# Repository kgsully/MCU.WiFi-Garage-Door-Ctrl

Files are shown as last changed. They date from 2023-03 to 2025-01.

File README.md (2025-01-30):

# WiFi Garage Door Controller
ESP32-WROOM Based WiFi enabled garage door controller design.

 Please refer to the README docx or PDF found in the documentation folder for further information.
 
 Schematics and drawings may be found within the documentation folder (dimensions are in mm). 
 
 3D design / printing models are located under the 'Enclosure' folder.

 Design updated for additional endpoint to allow for use with Apple Watch.
 
Imgur

Imgur

Imgur

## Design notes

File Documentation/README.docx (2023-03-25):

WiFi Garage Door Controller

Rev 1.1

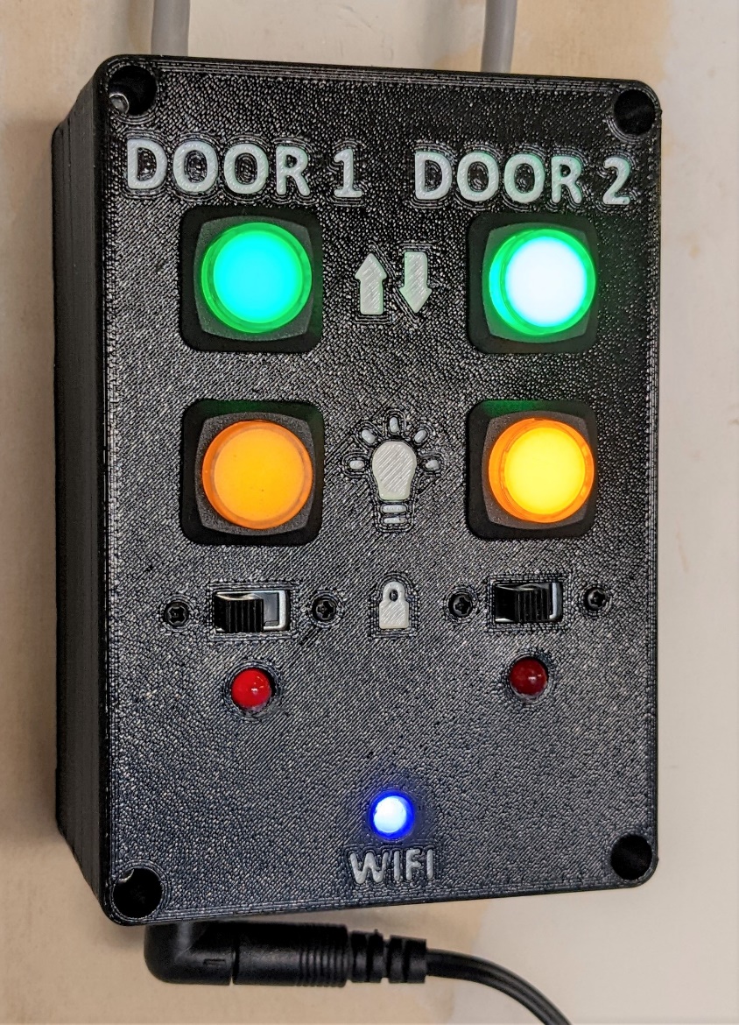
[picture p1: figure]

Ken S. 11/2022

# 1. Description

This is an ESP32-WROOM based design for a WiFi enabled garage door controller capable of operating 2 garage doors. It includes illuminated physical pushbuttons wired in parallel with relays to allow the user to operate the garage doors even if the controller is unpowered or disconnected from WiFi. Included controls mimic those found on the manufacturer provided openers for the units I have – Open/Close, Light On/Off, and Lock. The ESP32 acts as a webserver hosting a website with the applicable controls / status indications for both doors. This project uses the WiFi manager library to aid in WiFi connection and to prevent the need to hard-code the WiFi network credentials into the program. OTA update functionality is also included.

Design files are included for the following:

1. Controller Electrical Schematic (w/ manufacturer and P/N component properties)
2. Controller PCB Layout
3. Interactive PCB Bill of Materials (BOM) – HTML format
4. VS Code / PlatformIO based code
5. 3D Printed Enclosure

# 2. Electrical / PCB

The controller PCB uses 4 reed style relays wired in parallel with physical LED illuminated pushbuttons to control garage door operation. Off board connections use JST-PH style connectors. Please mind polarity (LEDs, etc.) when terminating off-board devices using the male JST-PH connectors.

‘Auto Program’ transistors are included in the design to prevent the need to press the ‘reset’ button after the code is uploaded to the microcontroller. Indication LEDs are generic 5mm THT LEDs.

The manufacturer provided garage door control pad(s) that this design is intended to emulate uses DC voltage only and a voltage divider circuit to determine which button has been pressed / whether the lock switches are set. Please refer to the notes in the addendum or electrical schematic for details. Determination of how your opener works is REQUIRED and resistance values / entire circuit design may need to be changed to accommodate your specific garage door controller!

Note that design accommodation for a UART pin header is included, but not required to be used due to the onboard USB – UART bridge IC.

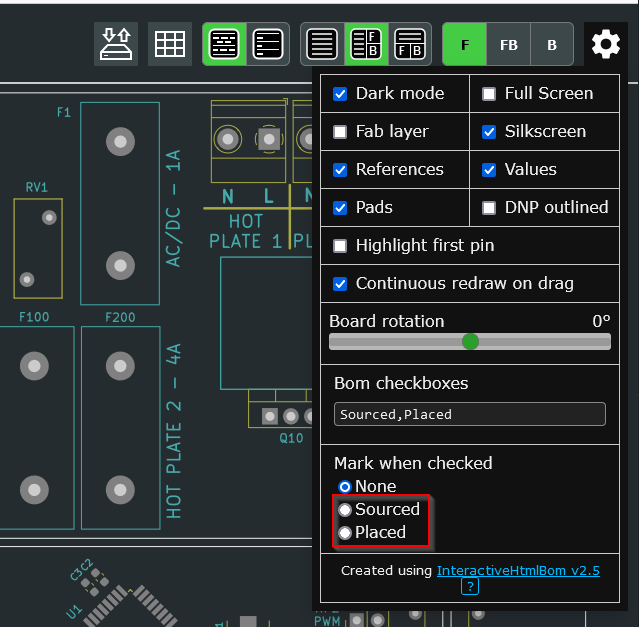
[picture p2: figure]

This design uses a Cypress / Infineon CY7C65213-28PVXI USB – UART bridge IC. The newer CY7C65213A-28PVXI may be used in its place. Please use the configuration utility that can be found at the following URL along with the included configuration file to program the USB – UART bridge:

https://www.infineon.com/cms/en/design-support/tools/configuration/usb-uart-config-utility/

Please refer to the included electrical schematic / PCB design / interactive BOM (html format) for further details. Note that selection of one of the options shown in the screenshot of the interactive BOM may be helpful during PCB assembly –

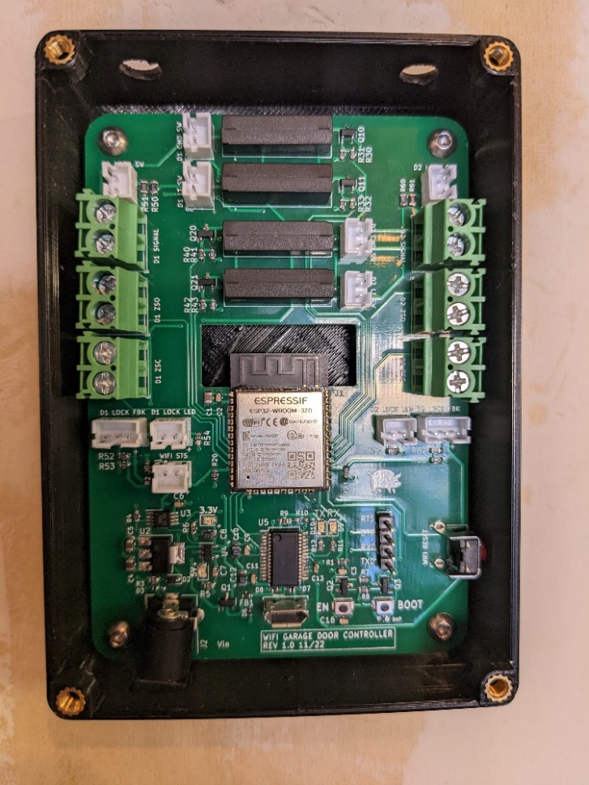
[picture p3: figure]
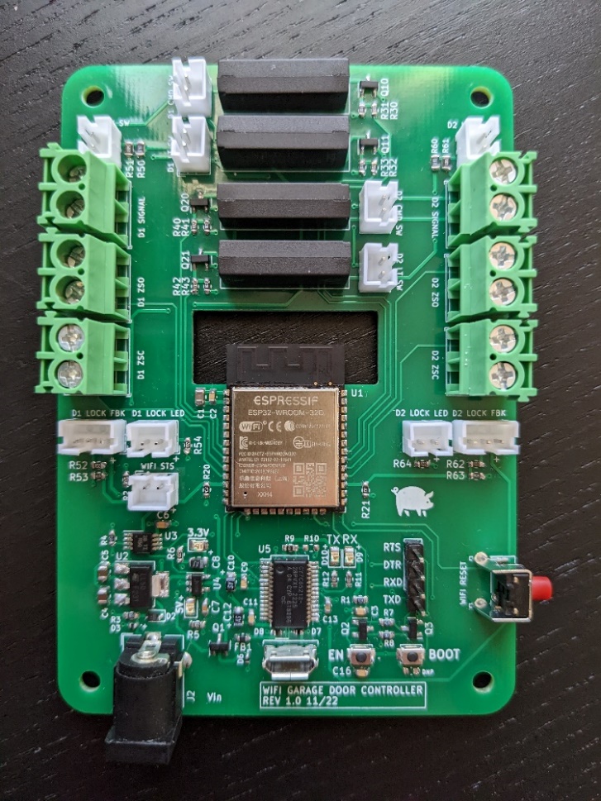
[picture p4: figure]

Completed PCB / Installation Pictures:

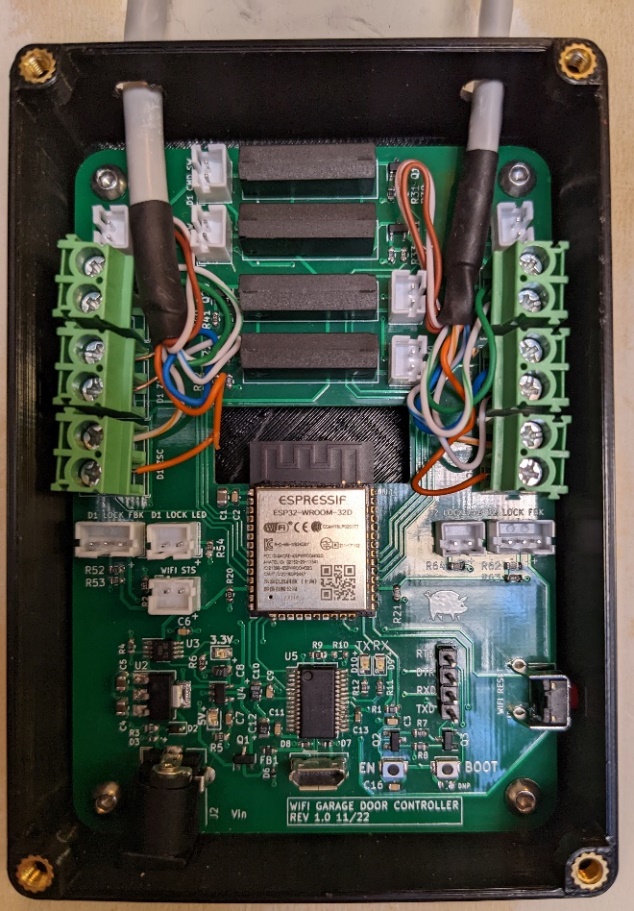
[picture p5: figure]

# 3. Assembly / Construction

Please refer to the included design files for assembly / construction details. Various format 3D models (STEP, F3D, and STL) are included, along with assembly / enclosure component drawings.

Drill holes in top of enclosure bottom of appropriate size for incoming wiring prior to mounting enclosure to the wall. Mount enclosure to the wall prior to mounting PCB in enclosure. CAT5 ethernet cable may be used to provide 8 conductors (2 spare).

NOTE: M3 Threaded heat press inserts are required for PCB mounting holes and enclosure top mounting holes (shown in pictures from previous section). Holes for PCB mounting and enclosure top mounting are sized in the 3D model to accept these inserts – fasteners will not thread into these holes due to their diameters.

# 4. Microcontroller Code

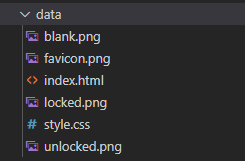
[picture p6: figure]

VS Code / PlatformIO must be used to upload the code to the microcontroller unless the user creates and Arduino IDE version. Note that for upload, there are additional files that must be uploaded to the ESP32 file structure (SPIFFS) – these can be found in the ‘data’ directory in the project. To upload to SPIFFS, select the PlatformIO icon on the left side bar, then select ‘Build’ and then ‘Upload’:

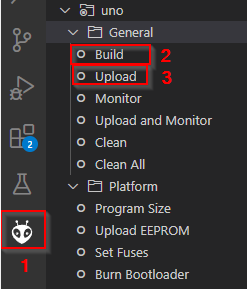
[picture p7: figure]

The code uses the following libraries:

1. Arduino.h
2. WiFi.h
3. ESPAsyncWebServer.h
4. WebSocketsServer.h
5. AsyncElegantOTA.h
6. ArduinoJson.h
7. SPIFFS.h

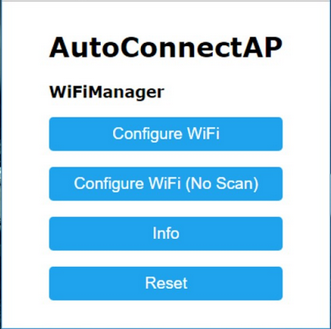
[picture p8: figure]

8. StreamString.h

If a WiFi network has not been configured, upon power up the ESP32 will operate in Access Point (AP) mode and hosts a website that scans for available WiFi networks and allows the user to select and provide credentials to connect. Once saved, this information is retained by the ESP32, even after a power cycle. It is suggested to set a static IP address for the ESP32 in your router configuration to ensure the IP address always remains the same.
The WiFi manager portal is configured to use the default http port of 80 for ease of use and connection.

There is a ‘WiFi’ reset button included in the design on the right side of the PCB that when pressed, will reset the WiFi connection configuration and re-enable WiFi manager.

Once connected to a WiFi network, WiFi manager will be disabled and the ESP32 will operate in station mode and automatically connect to the configured WiFi network upon power up.

The web page used for control and monitoring uses port 8080. This site is hosted by the ESP32 and can be modified by updating the index.html and style.css files contained in the project. It uses web sockets to pass JSON messages between the web page and the control code running in the ESP32. The web sockets server is set to use port 8081.

# 5. Operation / Usage

The controller can be powered via the 2.1mm barrel jack connector with a readily available 9VDC or 12VDC AC to DC converter - Ensure correct polarity of jack connection before purchase (positive on the inside).

The physical pushbuttons may be used in parallel with the web page to control garage door functions. Note that the lock functionality can only be toggled with the physical switch.

Control Over WiFi -

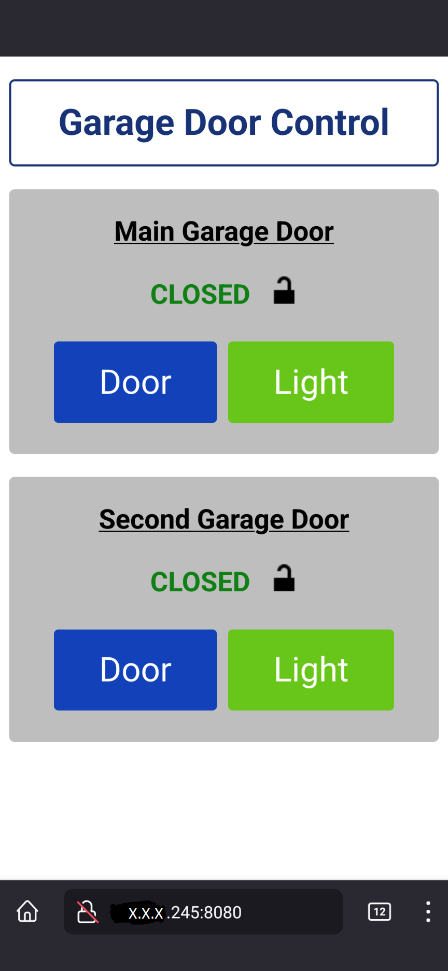
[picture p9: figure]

To connect to the control web page, navigate in a browser (computer or mobile device) to the IP address of the controller with the port suffix ‘:8080’ (e.g. 192.168.1.245:8080 - see screenshot).

Indicators / controls on the web page allow the user to monitor the current open or closed state of the garage door, whether the lock switch is set, and buttons are provided to issue an open / close command (‘Door’ button) or turn the light on or off (‘Light’ button). If the limit switches are in a state where neither is made, the indicator will display ‘Transition’, if both switches are made simultaneously, it will display ‘FAULT’.

If your device has been disconnected from the WiFi network the garage door controller is connected to, a page refresh may be required for status to update / commands to issue to the controller.

OTA Updates –

Program code as well as SPIFFS file system files can be updated ‘Over the Air’ (OTA) without the requirement to connect via USB. The file format required for OTA updates (both program and SPIFFS files) is .bin and must be created from the IDE before upload.

To use the OTA Update function, navigate to the IP_Address:Port (8080)/update (e.g. 192.168.1.245:8080/update - see screenshot).

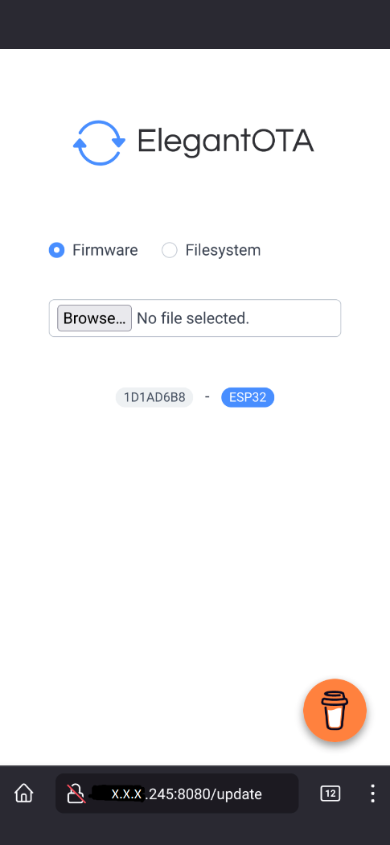
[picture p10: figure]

# 6. Addendum

Door Interface Notes:

Measured Voltages:
Door 1: ~ 5 VDC (No AC)
Door 2: ~ 18 VDC (No AC)

Measured Resistances (same for both doors):
Unlocked:
No Buttons Open Line
Command Button < 1 ohm (short)
Light Button ~ 204 ohms

Locked:
No Buttons ~83 ohms
Command Button < 1 ohm (short)
Light Button ~ 83 ohms

Links / Part Numbers for various off-board / supporting parts:

DC Barrel Jack Connector – 2.1mm:
Adafruit PID 373
https://www.adafruit.com/product/373

Door Switches (Green):
Adafruit PID 1440
https://www.adafruit.com/product/1440

Door Switches (Yellow / Amber):
Adafruit PID 1441
https://www.adafruit.com/product/1441

Lock Slide Switches:
Nidec Copal - MFS201N-Z
https://www.digikey.com/en/products/detail/nidec-copal-electronics/MFS201N-Z/5086556

Door Limit Switches (Generic):
https://a.co/d/92kAZzZ

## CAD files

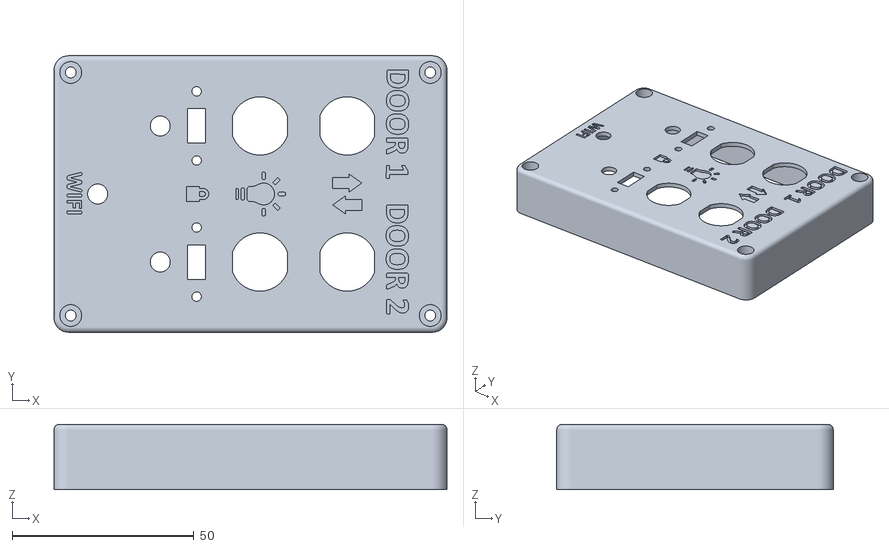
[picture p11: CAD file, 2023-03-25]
Enclosure/3D Printing/Model/Enclosure_Top.stl
108.0 x 76.0 x 18.0

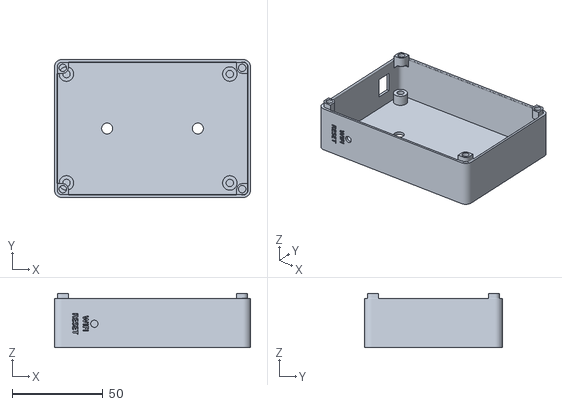
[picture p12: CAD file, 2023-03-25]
Enclosure/3D Printing/Model/Enclosure_Bottom.stl
108.0 x 76.0 x 30.0

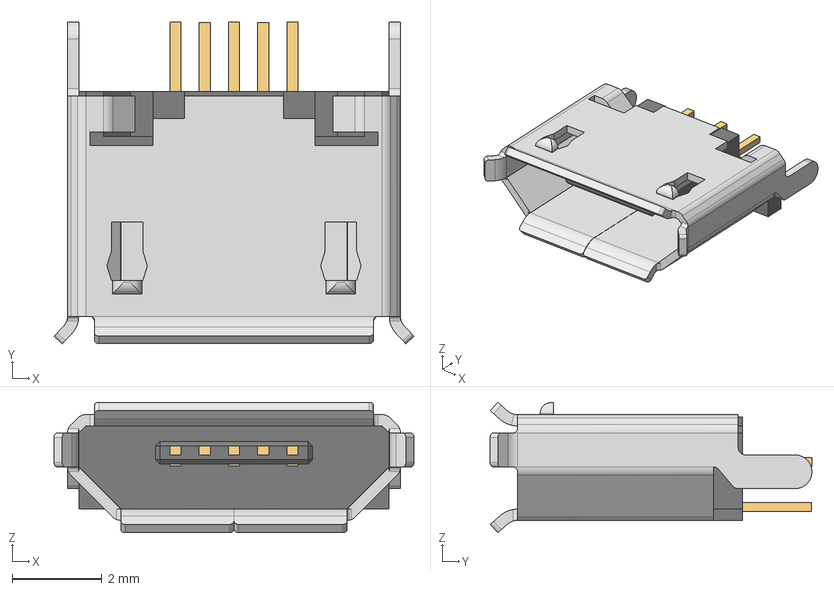
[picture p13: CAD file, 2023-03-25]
Electrical & PCB/Models/614105150721 (rev1).stp
8.00 x 7.15 x 2.90 mm
614105150721_Housing
614105150721_Pin1 x 3
614105150721_Pin2 x 2
614105150721_Shielding

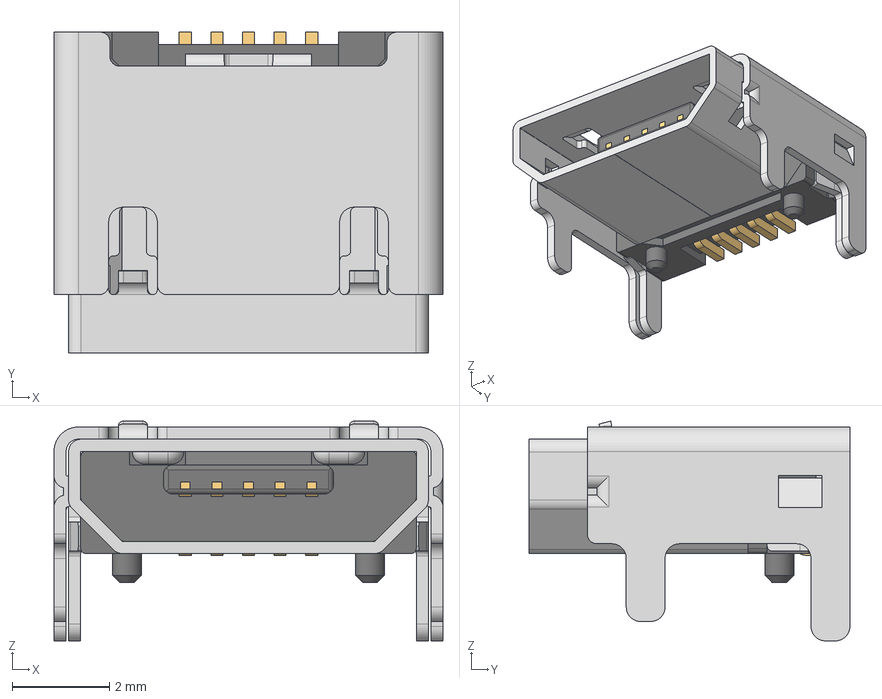
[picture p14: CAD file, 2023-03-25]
Electrical & PCB/Models/629105150521 (rev1).stp
8.00 x 6.60 x 4.52 mm
629105150521_Housing
629105150521_Pin1 x 4
629105150521_Pin2
629105150521_Shielding2
629105150521_Shielding

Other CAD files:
Enclosure/Model/Garage Door Controller Enclosure.f3d

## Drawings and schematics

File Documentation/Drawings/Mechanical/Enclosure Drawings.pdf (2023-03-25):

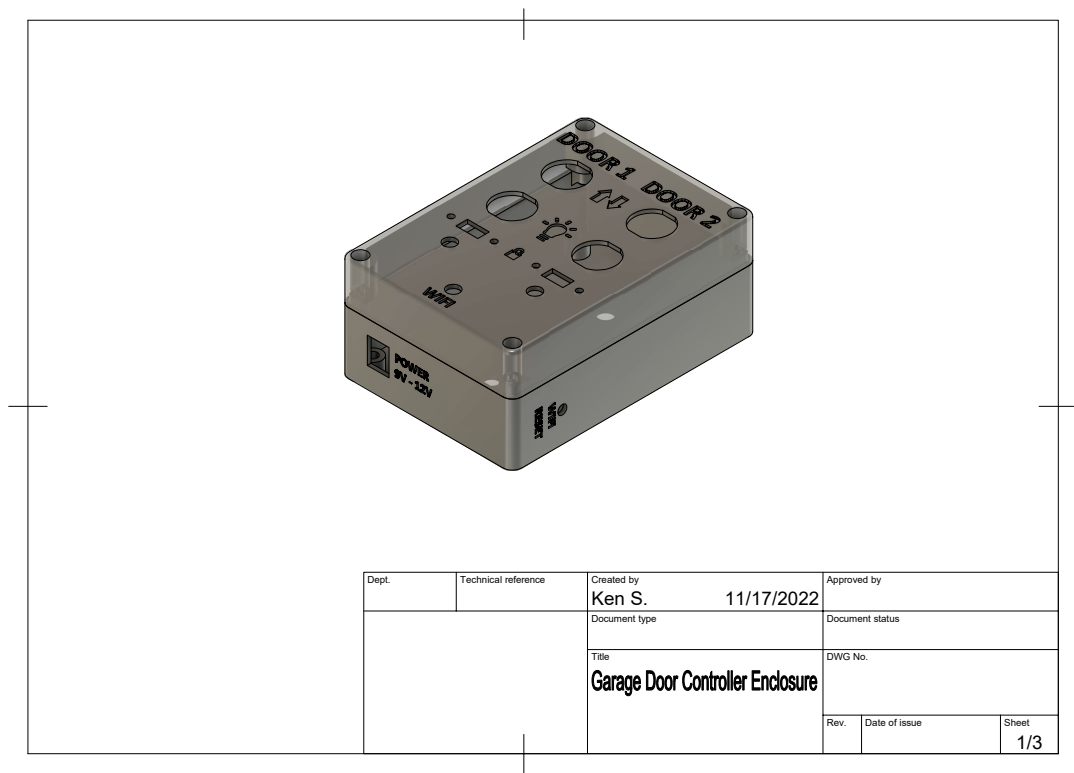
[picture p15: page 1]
Dept.; Technical reference; Created by; Approved by Document type; Document status Title; DWG No. Rev.; Date of issue; Sheet 11/17/2022; 1/3 Ken S.

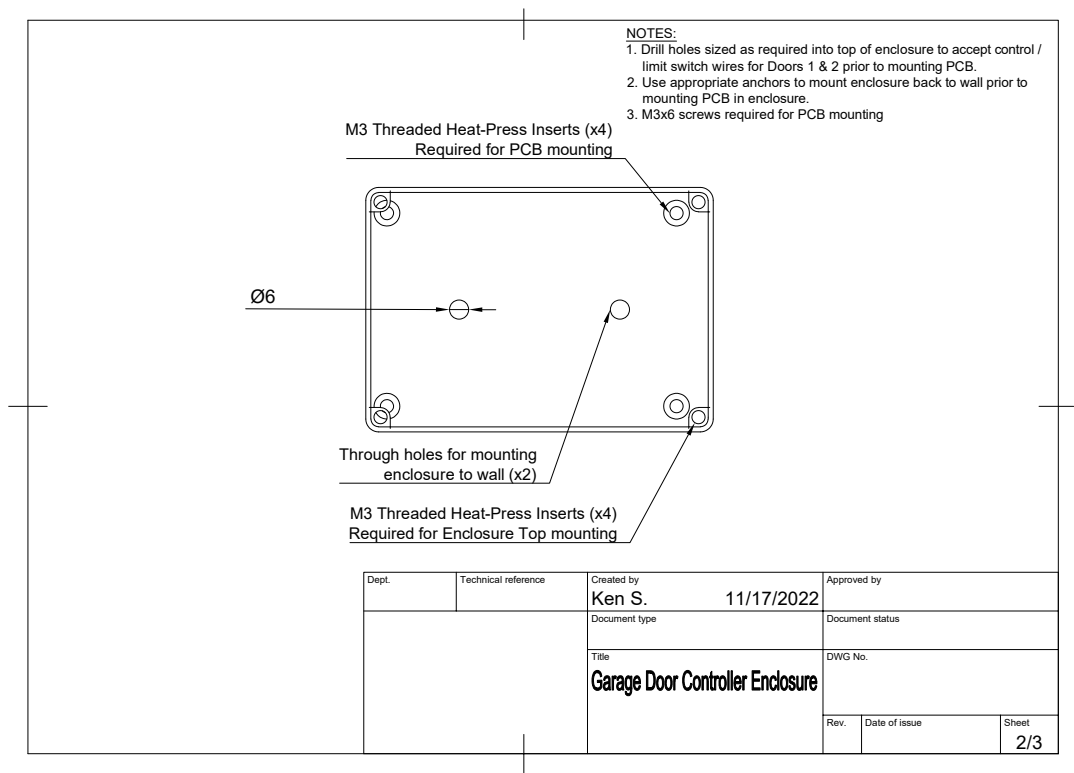
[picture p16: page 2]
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

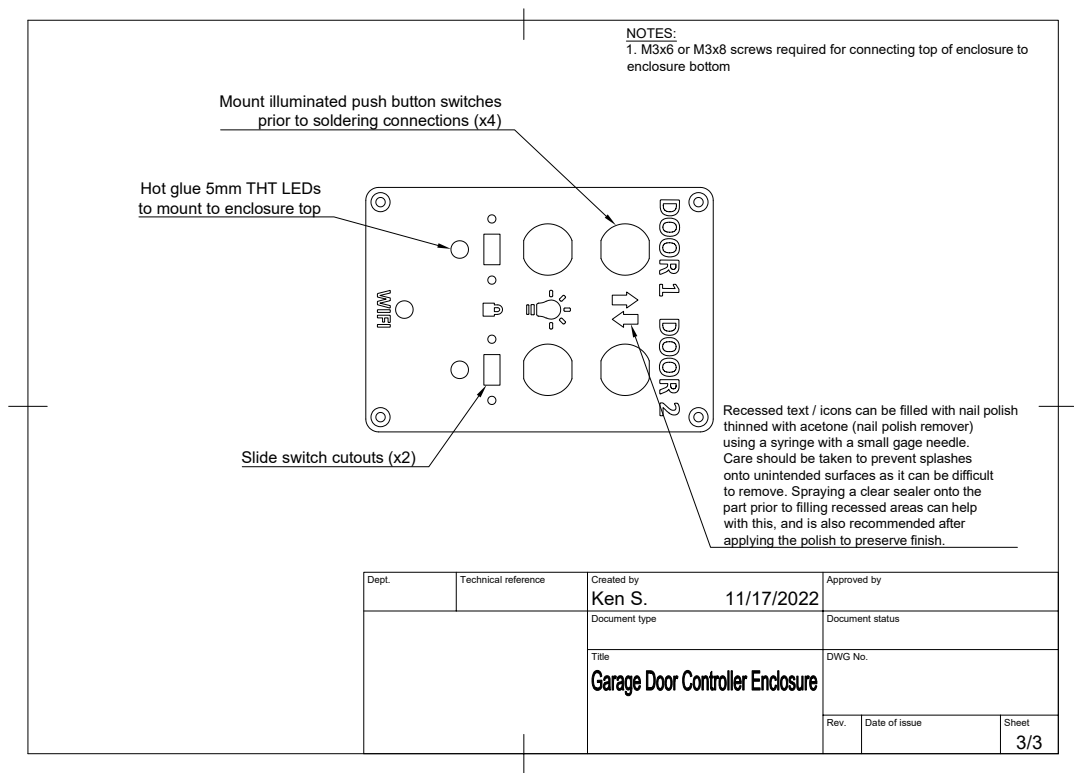
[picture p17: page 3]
Dept.; Technical reference; Created by; Approved by Document type; Document status Title; DWG No. Rev.; Date of issue; Sheet 11/17/2022; 3/3 Ken S. Mount illuminated push button switches prior to soldering connections (x4) Slide switch cutouts (x2) Hot glue 5mm THT LEDs to mount to enclosure top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

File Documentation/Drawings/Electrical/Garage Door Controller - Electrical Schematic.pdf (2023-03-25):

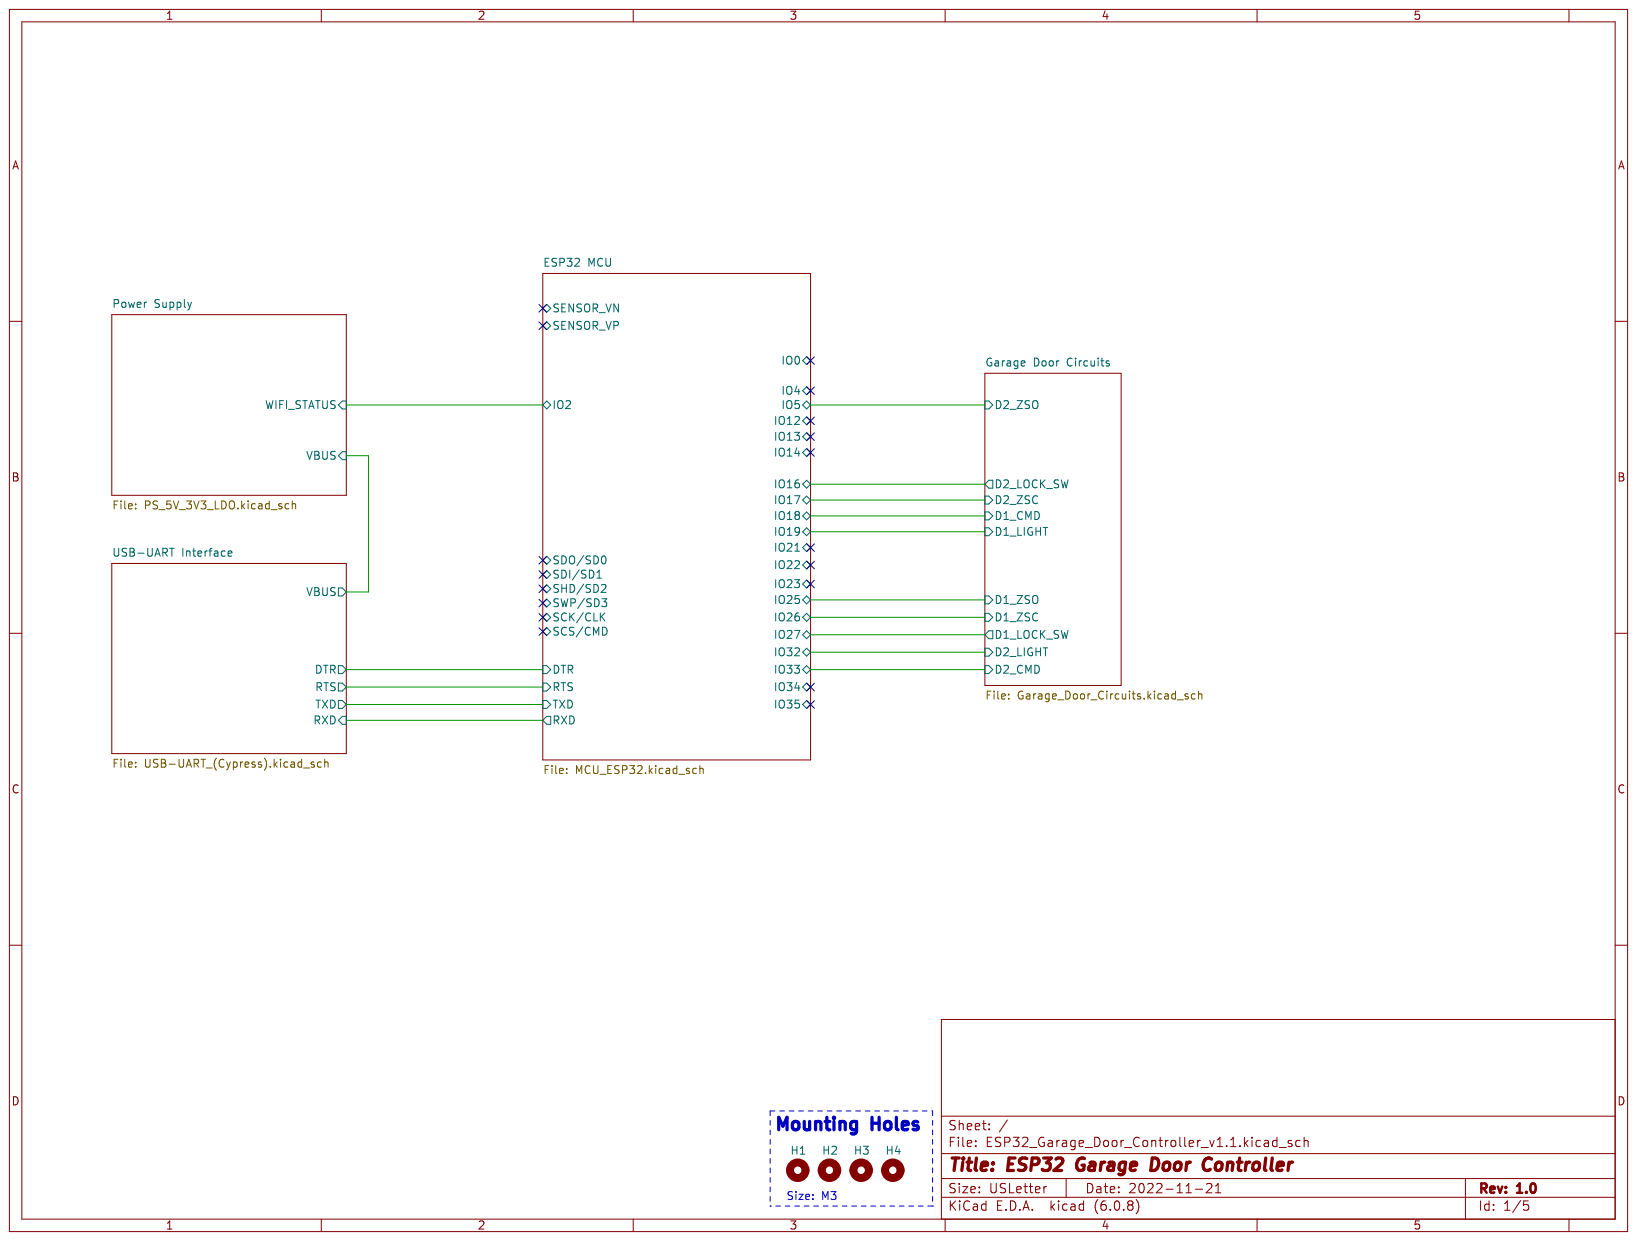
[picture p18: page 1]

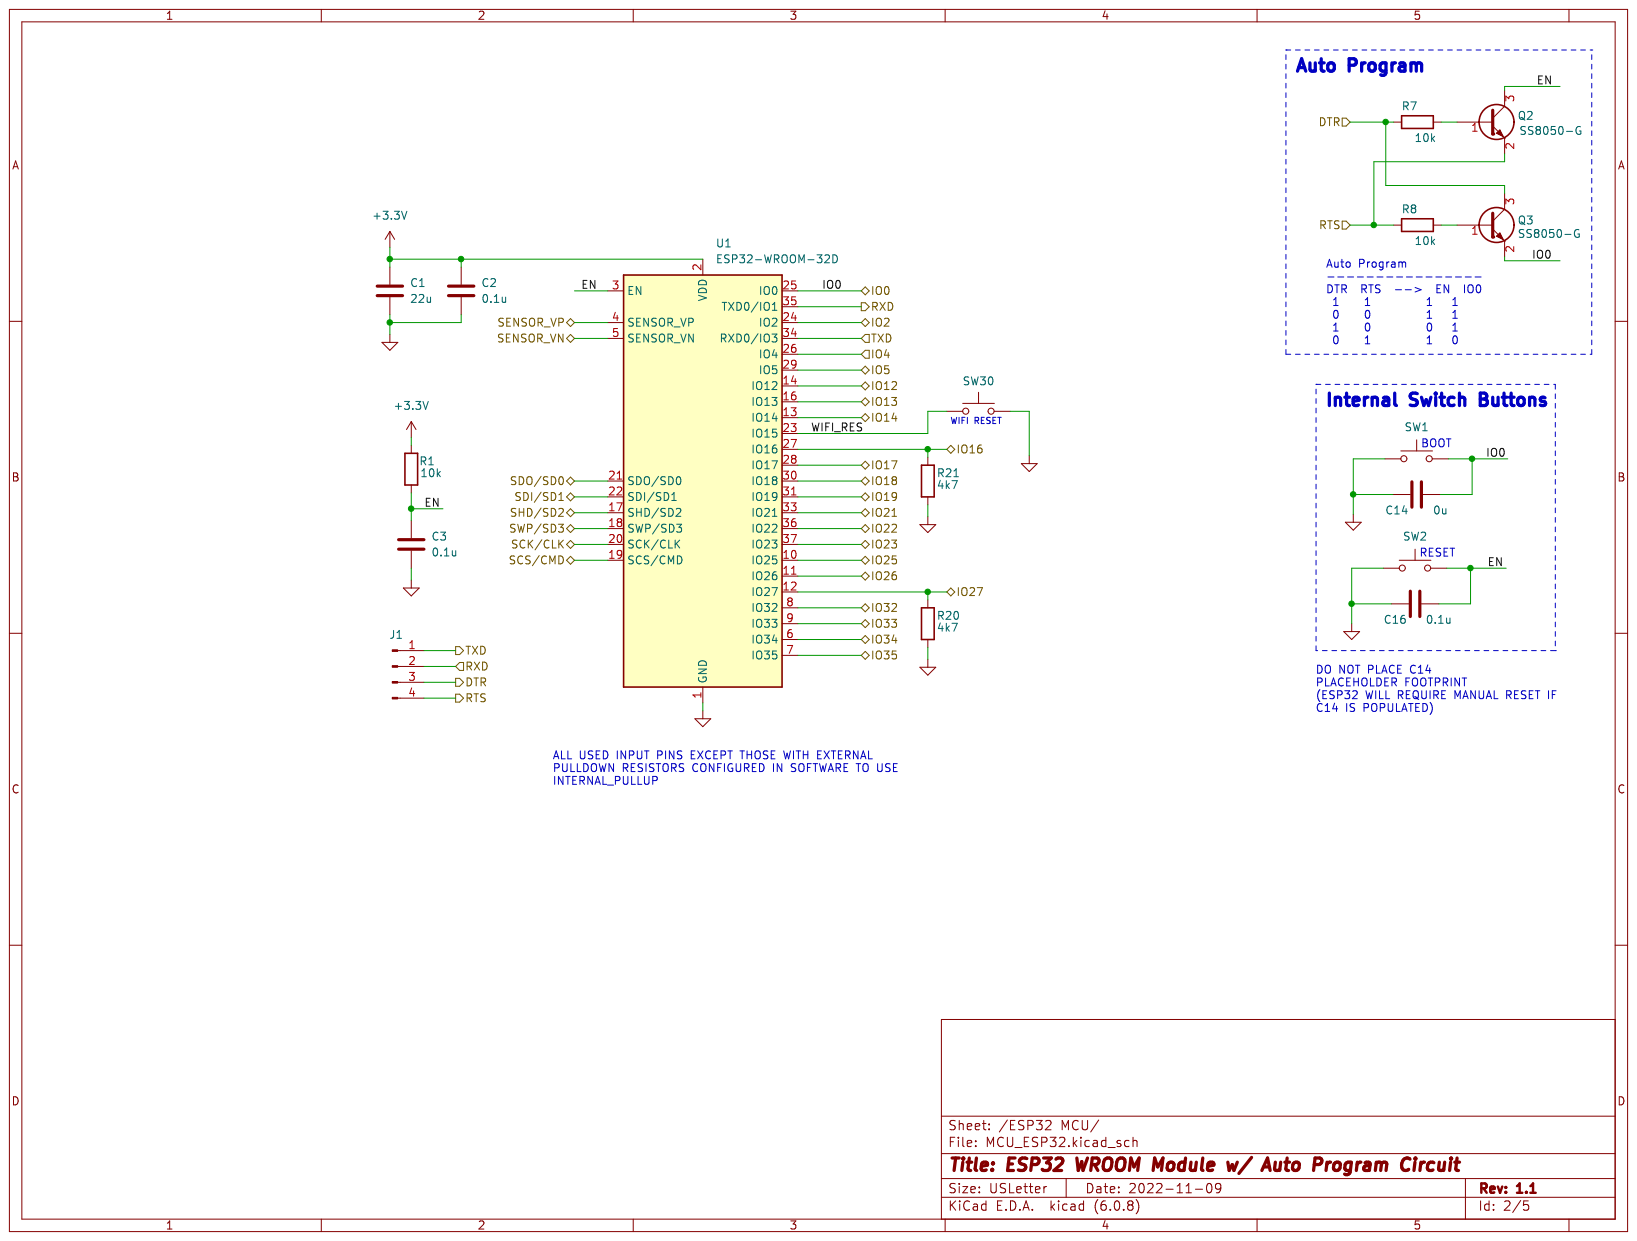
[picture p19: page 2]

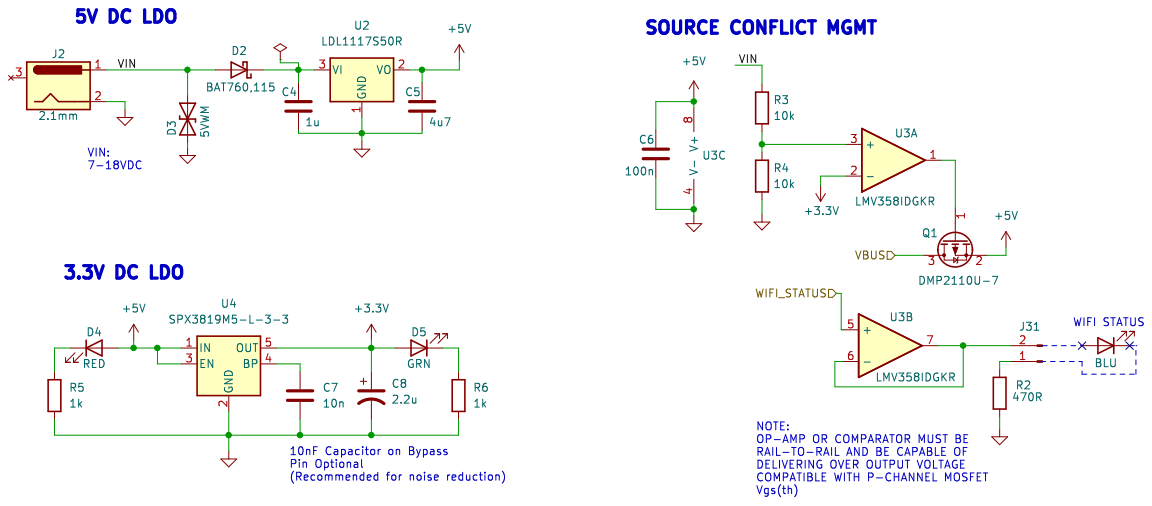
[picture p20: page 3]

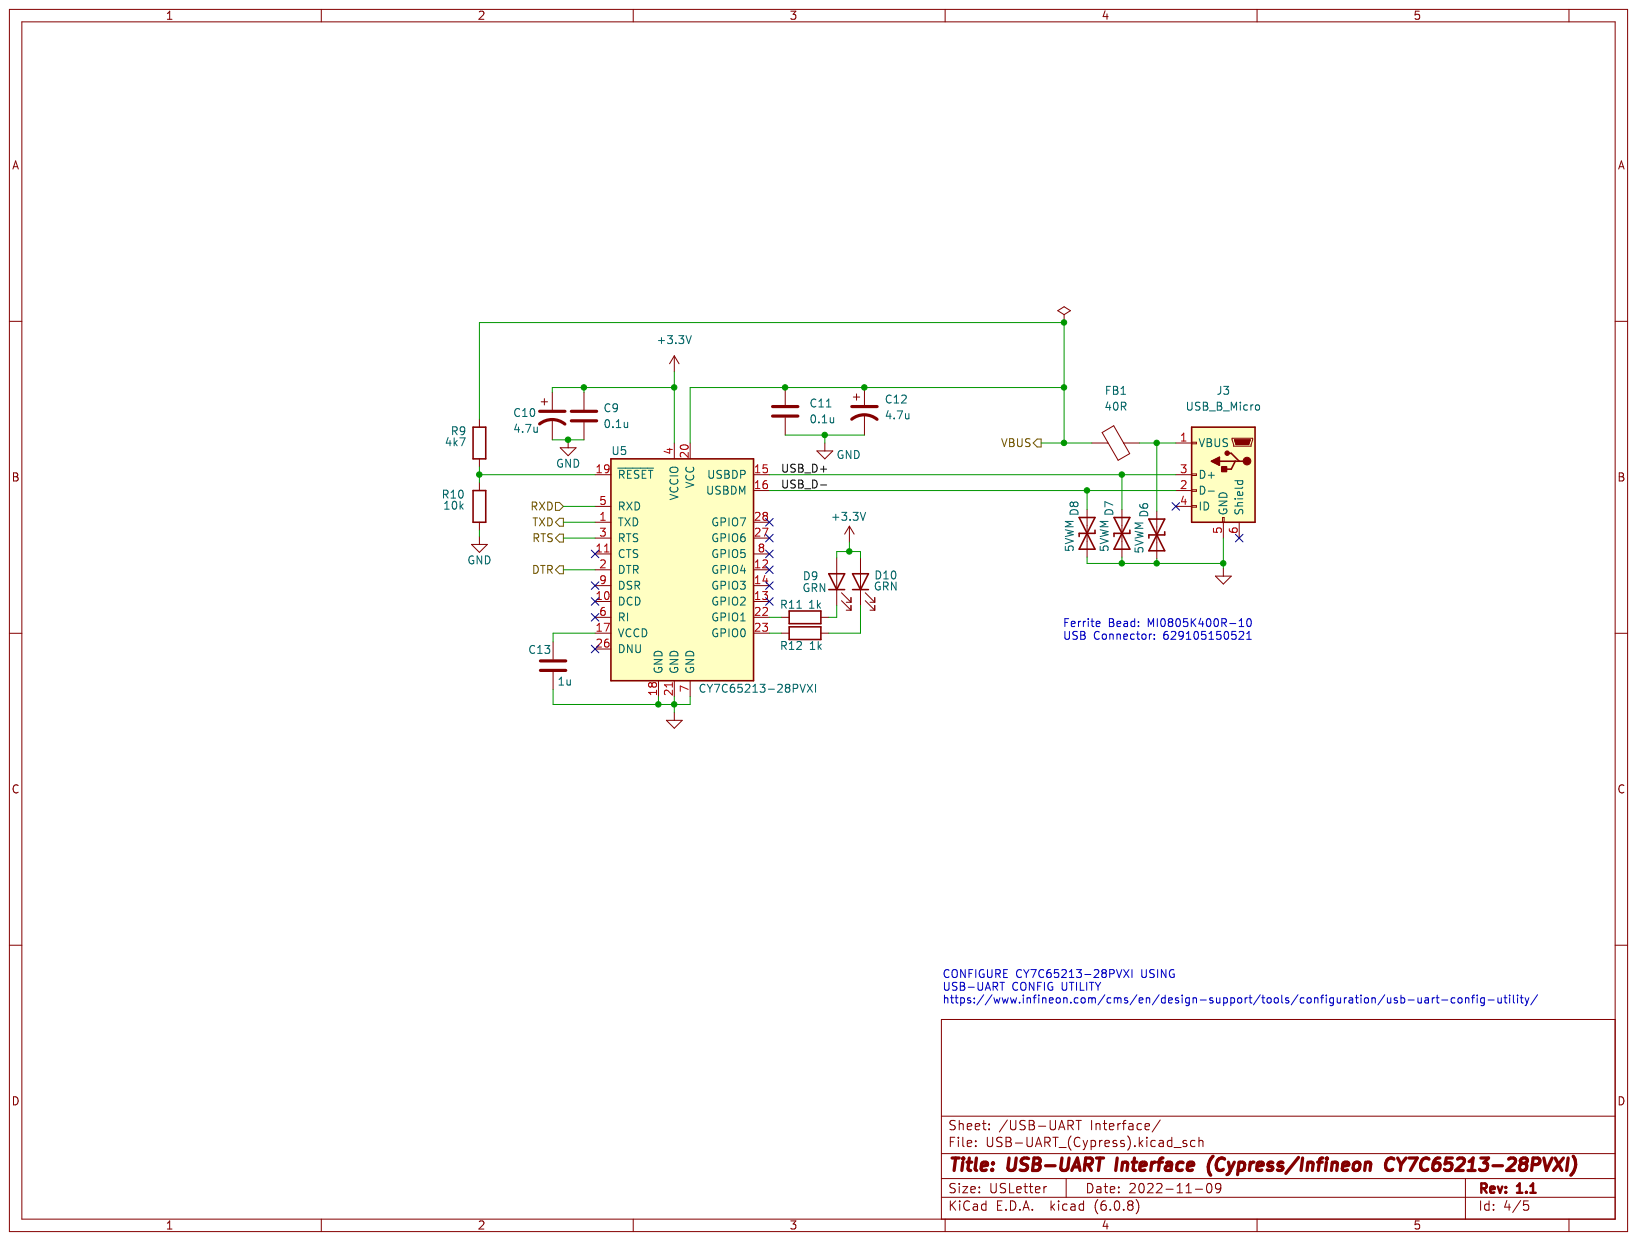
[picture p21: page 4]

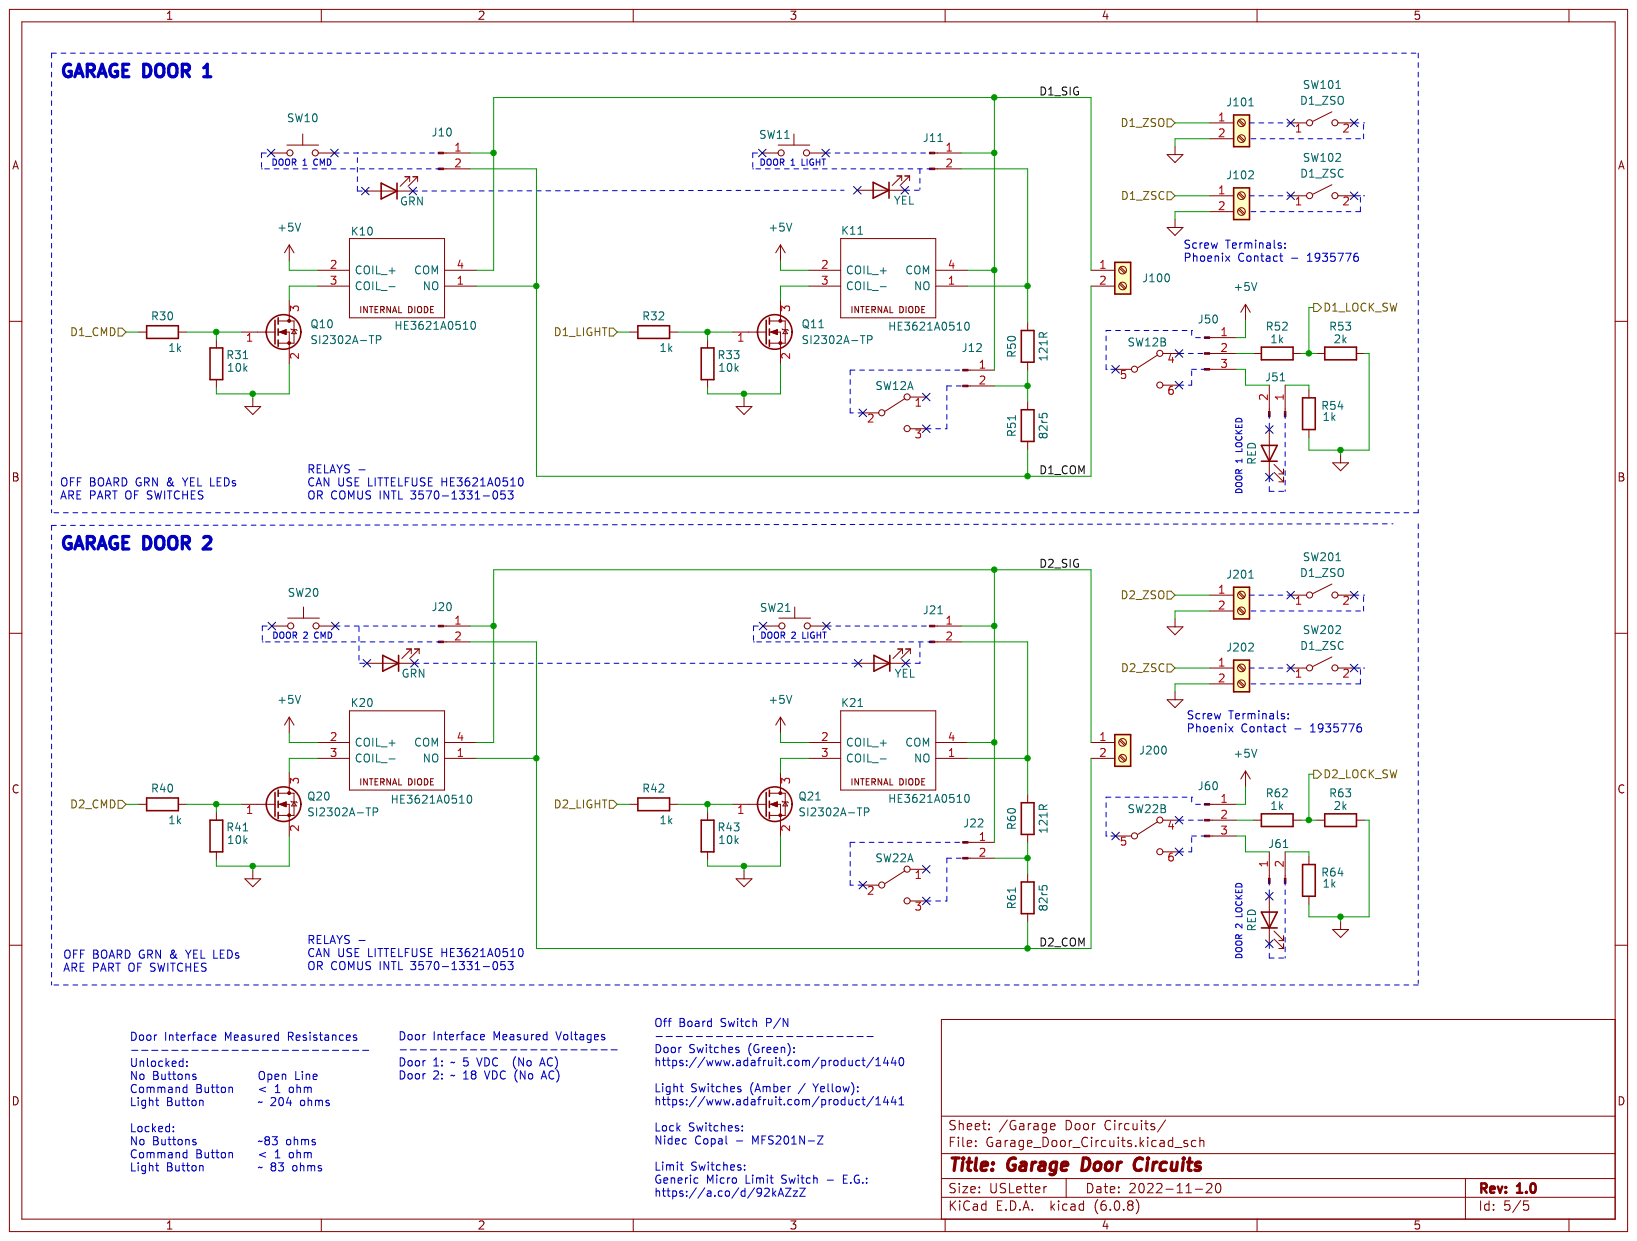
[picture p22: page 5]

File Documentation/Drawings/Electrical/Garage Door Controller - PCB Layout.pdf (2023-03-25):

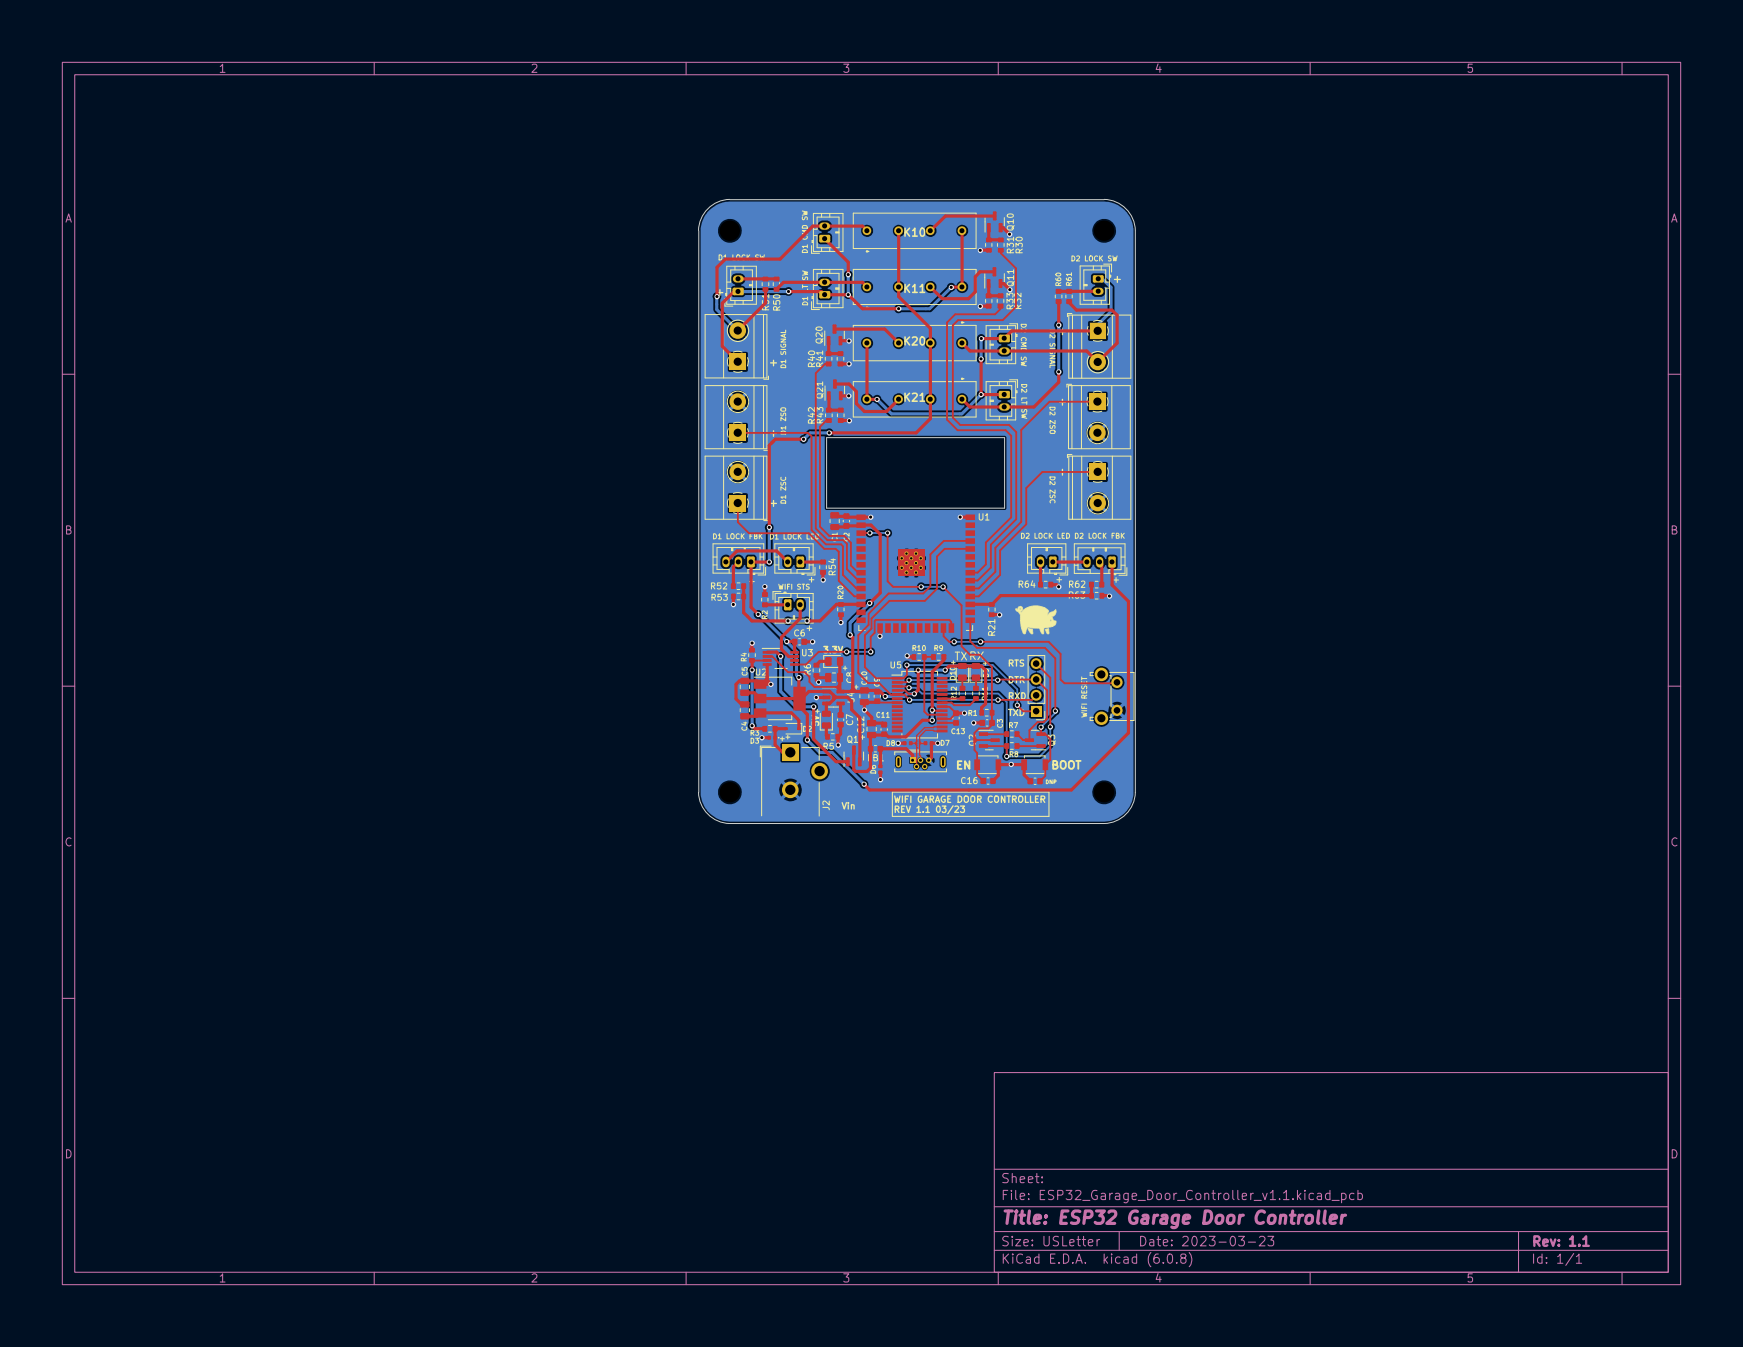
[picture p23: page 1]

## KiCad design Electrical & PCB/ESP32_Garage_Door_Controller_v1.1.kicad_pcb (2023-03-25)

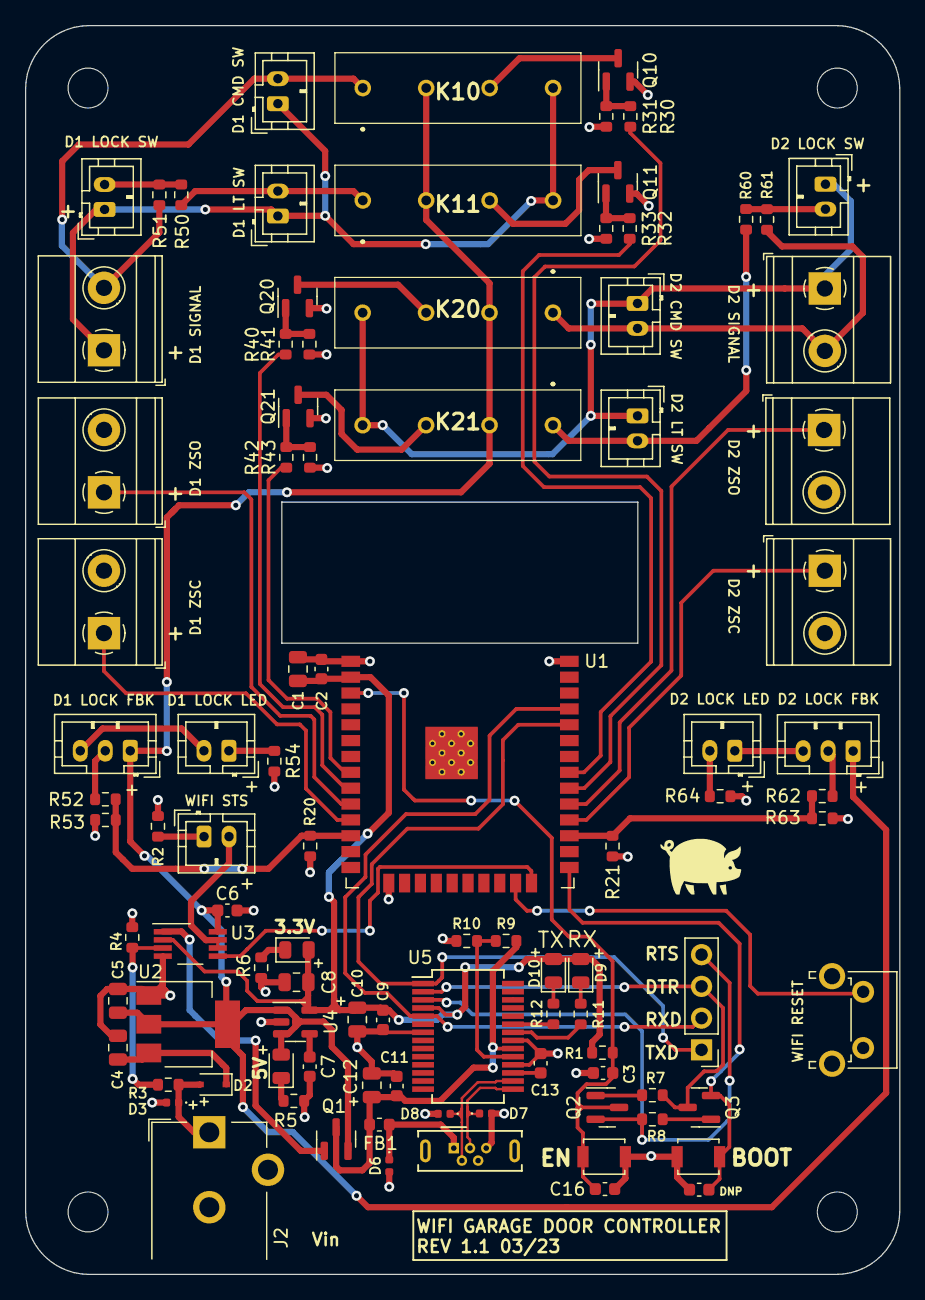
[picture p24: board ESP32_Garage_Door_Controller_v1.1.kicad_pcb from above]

Board: 2 copper layers, 70.0 x 100.0 mm, 100 parts (0 on the bottom side), 64 nets.

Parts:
C1: 22u; C_0805_2012Metric
C2, C3, C9, C11, C16: 0.1u; C_0603_1608Metric
C4: 1u; C_0805_2012Metric
C5: 4u7; C_0805_2012Metric
C6: 100n; C_0603_1608Metric
C7: 10n; C_0603_1608Metric
C8: 2.2u; C_0805_2012Metric
C10, C12: 4.7u; C_0805_2012Metric
C13: 1u; C_0603_1608Metric
C14: 0u; C_0603_1608Metric
D2: BAT760,115; D_SOD-323
D3, D6, D7, D8: 5VWM; D_0402_1005Metric
D4: RED; LED_0805_2012Metric
D5, D9, D10: GRN; LED_0805_2012Metric
FB1: 40R; L_0603_1608Metric
H1, H2, H3, H4: MountingHole; MountingHole_3.2mm_M3
J1: Conn_01x04_Male; PinHeader_1x04_P2.54mm_Vertical
J2: 2.1mm; BarrelJack_CUI_PJ-102AH_Horizontal
J3: USB_B_Micro; USB_Micro-B_Wuerth_614105150721_Vertical
J10, J11, J12, J20, J21, J22, J31, J51, J61: Conn_01x02_Male; JST_PH_B2B-PH-K_1x02_P2.00mm_Vertical
J50, J60: Conn_01x03_Male; JST_PH_B3B-PH-K_1x03_P2.00mm_Vertical
J100, J101, J102, J200, J201, J202: 1935776; TerminalBlock_Phoenix_MKDS-1,5-2_1x02_P5.00mm_Horizontal
K10, K11, K20, K21: HE3621A0510
Q1: DMP2110U-7; SOT-23
Q2, Q3: SS8050-G; SOT-23
Q10, Q11, Q20, Q21: SI2302A-TP; SOT-23
R1, R3, R4, R7, R8, R10, R31, R33, R41, R43: 10k; R_0603_1608Metric
R2: 470R; R_0603_1608Metric
R5, R6, R11, R12, R30, R32, R40, R42, R52, R54, R62, R64: 1k; R_0603_1608Metric
R9, R20, R21: 4k7; R_0603_1608Metric
R50, R60: 121R; R_0603_1608Metric
R51, R61: 82r5; R_0603_1608Metric
R53, R63: 2k; R_0603_1608Metric
SW1, SW2: SW_Push; SW_SPST_B3U-1000P
SW30: SW_Push; SW_Tactile_SPST_Angled_PTS645Vx58-2LFS
U1: ESP32-WROOM-32D; ESP32-WROOM-32
U2: LDL1117S50R; SOT-223-3_TabPin2
U3: LMV358IDGKR; VSSOP-8_3.0x3.0mm_P0.65mm
U4: SPX3819M5-L-3-3; SOT-23-5
U5: CY7C65213-28PVXI; SSOP-28_5.3x10.2mm_P0.65mm

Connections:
+3.3V: C1.1, C2.1, C8.1, C9.2, C10.1, D5.2 (A), D9.2 (A), D10.2 (A), R1.1, U1.2 (VDD), U3.2 (-), U4.5 (OUT), U5.4 (VCCIO)
+5V: C5.1, C6.1, D4.2 (A), J50.1, J60.1, K10.2 (COIL_+), K11.2 (COIL_+), K20.2 (COIL_+), K21.2 (COIL_+), Q1.2 (S), U2.2 (VO), U3.8 (V+), U4.1 (IN), U4.3 (EN)
/ESP32 MCU/DTR: J1.3, Q3.3 (C), R7.1, U5.2 (DTR)
/ESP32 MCU/EN: C3.1, C16.2, Q2.3 (C), R1.2, SW2.2, U1.3 (EN)
/ESP32 MCU/IO0: C14.2, Q3.2 (E), SW1.2, U1.25 (IO0)
/ESP32 MCU/IO2: U1.24 (IO2), U3.5 (+)
/ESP32 MCU/IO5: J201.1, U1.29 (IO5)
/ESP32 MCU/IO16: R21.1, R62.1, R63.2, U1.27 (IO16)
/ESP32 MCU/IO17: J202.1, U1.28 (IO17)
/ESP32 MCU/IO18: R30.1, U1.30 (IO18)
/ESP32 MCU/IO19: R32.1, U1.31 (IO19)
/ESP32 MCU/IO25: J101.1, U1.10 (IO25)
/ESP32 MCU/IO26: J102.1, U1.11 (IO26)
/ESP32 MCU/IO27: R20.1, R52.1, R53.2, U1.12 (IO27)
/ESP32 MCU/IO32: R42.1, U1.8 (IO32)
/ESP32 MCU/IO33: R40.1, U1.9 (IO33)
/ESP32 MCU/RTS: J1.4, Q2.2 (E), R8.2, U5.3 (RTS)
/ESP32 MCU/RXD: J1.2, U1.35 (TXD0/IO1), U5.5 (RXD)
/ESP32 MCU/TXD: J1.1, U1.34 (RXD0/IO3), U5.1 (TXD)
/ESP32 MCU/WIFI_RES: SW30.1, U1.23 (IO15)
/Garage Door Circuits/D1_COM: J10.2, J100.2, K10.1 (NO), R51.1
/Garage Door Circuits/D1_SIG: J10.1, J11.1, J12.1, J100.1, K10.4 (COM), K11.4 (COM)
/Garage Door Circuits/D2_COM: J20.2, J200.2, K20.1 (NO), R61.1
/Garage Door Circuits/D2_SIG: J20.1, J21.1, J22.1, J200.1, K20.4 (COM), K21.4 (COM)
/Power Supply/VBUS: C11.2, C12.1, FB1.2, Q1.3 (D), R9.2, U5.20 (VCC)
/Power Supply/VIN: D2.2 (A), D3.1 (A1), J2.1, R3.1
/USB-UART Interface/USB_D+: D7.1 (A1), J3.3 (D+), U5.15 (USBDP)
/USB-UART Interface/USB_D-: D8.1 (A1), J3.2 (D-), U5.16 (USBDM)
GND: C1.2, C2.2, C3.2, C4.2, C5.2, C6.2, C7.2, C8.2, C9.1, C10.2, C11.1, C12.2, C13.2, C14.1, C16.1, D3.2 (A2), D6.2 (A2), D7.2 (A2), D8.2 (A2), J2.2, J3.5 (GND), J101.2, J102.2, J201.2, J202.2, Q10.2 (S), Q11.2 (S), Q20.2 (S), Q21.2 (S), R2.2, R4.2, R5.2, R6.2, R10.1, R20.2, R21.2, R31.2, R33.2, R41.2, R43.2, R53.1, R54.2, R63.1, R64.2, SW1.1, SW2.1, SW30.2, U1.1 (GND), U1.15 (GND), U1.38 (GND), U1.39 (GND), U2.1 (GND), U3.4 (V-), U4.2 (GND), U5.7 (GND), U5.18 (GND), U5.21 (GND)
unnamed: C4.1, D2.1 (K), U2.3 (VI)
unnamed: C7.1, U4.4 (BP)
unnamed: C13.1, U5.17 (VCCD)
unnamed: D4.1 (K), R5.1
unnamed: D5.1 (K), R6.1
unnamed: D6.1 (A1), FB1.1, J3.1 (VBUS)
unnamed: D9.1 (K), R11.2
unnamed: D10.1 (K), R12.2
unnamed: J11.2, K11.1 (NO), R50.2
unnamed: J12.2, R50.1, R51.2
unnamed: J21.2, K21.1 (NO), R60.2
unnamed: J22.2, R60.1, R61.2
unnamed: J31.1, R2.1
unnamed: J31.2, U3.6 (-), U3.7
unnamed: J50.2, R52.2
unnamed: J50.3, J51.2
unnamed: J51.1, R54.1
unnamed: J60.2, R62.2
unnamed: J60.3, J61.1
unnamed: J61.2, R64.1
unnamed: K10.3 (COIL_-), Q10.3 (D)
unnamed: K11.3 (COIL_-), Q11.3 (D)
unnamed: K20.3 (COIL_-), Q20.3 (D)
unnamed: K21.3 (COIL_-), Q21.3 (D)
unnamed: Q1.1 (G), U3.1
unnamed: Q2.1 (B), R7.2
unnamed: Q3.1 (B), R8.1
unnamed: Q10.1 (G), R30.2, R31.1
unnamed: Q11.1 (G), R32.2, R33.1
unnamed: Q20.1 (G), R40.2, R41.1
unnamed: Q21.1 (G), R42.2, R43.1
unnamed: R3.2, R4.1, U3.3 (+)
unnamed: R9.1, R10.2, U5.19 (~RESET)
unnamed: R11.1, U5.22 (GPIO1)
unnamed: R12.1, U5.23 (GPIO0)

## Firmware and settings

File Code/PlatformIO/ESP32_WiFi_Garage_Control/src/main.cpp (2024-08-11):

/* 
ESP32 WiFi Garage Door Controller
by Ken S. 
Last updated: 08/2024
Original:     12/2022

Code for an ESP32-WROOM based design for a WiFi enabled garage door controller capable of operating 2 garage doors. 
It includes illuminated physical pushbuttons wired in parallel with relays to allow the user to operate the 
garage doors even if the controller is unpowered or disconnected from WiFi. 
Included controls mimic those found on the manufacturer provided openers for the units I have – Open/Close, Light On/Off, and Lock. 
The ESP32 acts as a webserver hosting a website with the applicable controls / status indications for both doors. 
This project uses the WiFi manager library to aid in WiFi connection and to prevent the 
need to hard-code the WiFi network credentials into the program. OTA update functionality is also included.

Update - 08/2024:
- Refactor to separate Javascript into app.js
- Added functionality for a minimal version of the website providing only door controls without feedback display.
  This is intended to be used with an apple watch, whose webkit (at the time of this writing) has little / no
  javascript support. As a result, transactions between the web front-end and the MCU backend are accomplished
  via form submission and conditionals based upon the parameter key/value pair. Create a shortcut on the apple
  watch (Open URL --> [deviceURL]/watch) in order to open the website.


THIS SOFTWARE IS PROVIDED ''AS IS'' AND ANY
EXPRESS OR IMPLIED WARRANTIES, INCLUDING, BUT NOT LIMITED TO, THE IMPLIED
WARRANTIES OF MERCHANTABILITY AND FITNESS FOR A PARTICULAR PURPOSE ARE
DISCLAIMED. IN NO EVENT SHALL THE AUTHOR(S) BE LIABLE FOR ANY
DIRECT, INDIRECT, INCIDENTAL, SPECIAL, EXEMPLARY, OR CONSEQUENTIAL DAMAGES
(INCLUDING, BUT NOT LIMITED TO, PROCUREMENT OF SUBSTITUTE GOODS OR SERVICES;
LOSS OF USE, DATA, OR PROFITS; OR BUSINESS INTERRUPTION) HOWEVER CAUSED AND
ON ANY THEORY OF LIABILITY, WHETHER IN CONTRACT, STRICT LIABILITY, OR TORT
(INCLUDING NEGLIGENCE OR OTHERWISE) ARISING IN ANY WAY OUT OF THE USE OF THIS
SOFTWARE, EVEN IF ADVISED OF THE POSSIBILITY OF SUCH DAMAGE.  
*/

#include <Arduino.h>
#include <WiFi.h>
#include <WiFiManager.h>
#include <ESPAsyncWebServer.h>
#include <WebSocketsServer.h>
#include <AsyncElegantOTA.h>
#include <ArduinoJson.h>
#include <SPIFFS.h>
#include <StreamString.h>

// GPIO Definitions
#define pin_wifiReset 15
#define pin_wifiStatus 2

#define pin_door1CMD 18
#define pin_door1Light 19
#define pin_door1LockSW 27
#define pin_door1ZSO 25
#define pin_door1ZSC 26

#define pin_door2CMD 33
#define pin_door2Light 32
#define pin_door2LockSW 16 
#define pin_door2ZSO 5
#define pin_door2ZSC 17

// Variable Definitions
bool door1_CMD = 0;
bool door1_Light = 0;
bool door1_ZSO = 0;
bool door1_ZSC = 0;
bool door1_LockSts = 0;
bool door2_CMD = 0;
bool door2_Light = 0;
bool door2_ZSO = 0;
bool door2_ZSC = 0;
bool door2_LockSts = 0;

bool door1_CMD_Latch = 0;
bool door1_Light_Latch = 0;
bool door2_CMD_Latch = 0;
bool door2_Light_Latch = 0;

bool pageLoadTrigger = 0;

int cmdHoldPeriod = 1000;
unsigned long door1_CMD_Time = 0;
unsigned long door1_Light_Time = 0;
unsigned long door2_CMD_Time = 0;
unsigned long door2_Light_Time = 0;
unsigned long wifi_Previous_Time = 0;
unsigned long wifi_Reconnect_Delay = 20000;

int doorStatus[6] = {0, 0, 0, 0, 0, 0};
int doorStatusBuffer[6] = {0, 0, 0, 0, 0, 0};

// Create WifiManager Object
WiFiManager wm;
//wm.setHttpPort(83);  // If necessary to change the WiFi Manager portal port use this

// Create WebServer and WebSocket Server Objects w/ Port #'s
AsyncWebServer webServer(8080); 
WebSocketsServer webSocketsServer(8081); 

const char* wm_SSID = "ESP32 WiFi Manager";
const char* wm_Password = "wmPassword";

void wifiInit() {
  WiFi.mode(WIFI_STA);  // Use if configuring for station mode, comment out if using AP mode

  bool res;
  res = wm.autoConnect(wm_SSID); // For a password protected AP, syntax is as follows wm.autoConnect(wm_SSID, wm_Password)
  if(!res) {
    Serial.println("Failed to Connect");
    // ESP.restart();
  }
  else {
    Serial.println("");
    Serial.println("WiFi Connected");
    Serial.print("IP Address: ");
    Serial.println(WiFi.localIP());
  }
  //wm.resetSettings();  // Reset WiFi settings and use manager AP
}

void notFound(AsyncWebServerRequest *request) {
  request->send_P(404, "text/plain", "Not Found");  // send_P used as the webpage is stored in Program Memory (flash) instead of RAM
}

// WebSocket Server Event Handling
void webSocketsEvent(uint8_t clientNum, WStype_t type, uint8_t * payload, size_t length) {
  switch(type) {
    
    case WStype_DISCONNECTED:
      Serial.printf("[%u] - Disconnected\n", clientNum);
      break;
    
    case WStype_CONNECTED: {
      IPAddress clientIP = webSocketsServer.remoteIP(clientNum);
      Serial.printf("[%u] Connected from %d.%d.%d.%d url: %s\n", clientNum, clientIP[0], clientIP[1], clientIP[2], clientIP[3], payload);
      }
      break;
    
    case WStype_TEXT: {
      Serial.printf("Feedback JSON Data from Website: [%u] Text: %s\n", clientNum, payload);
      String message = String((char*)(payload));
      //Serial.println(message);

      DynamicJsonDocument JSON_Recv(200);                                       // De-serialize the data
      DeserializationError jsonError = deserializeJson(JSON_Recv, message);     // Parse the parameters we expect to receive and test if the parsing succeeds
      
      if (jsonError) {
        Serial.print("deserializeJson() failed: ");
        Serial.println(jsonError.c_str());
        return;
      }

      pageLoadTrigger = JSON_Recv["LoadTrigger"];                               // Set parameter values received from Website 
      door1_CMD       = JSON_Recv["door1_CMD"];
      door1_Light     = JSON_Recv["door1_Light"];
      door2_CMD       = JSON_Recv["door2_CMD"];
      door2_Light     = JSON_Recv["door2_Light"];
    }
      break;
  }
}

// Send JSON Data to webpage through WebSockets - JSON Formatting: {"VARIABLE" : VALUE}
void sendJSONData() {
  StreamString JSON_Send;
  StaticJsonDocument<200> JSON_Send_Temp;
  JSON_Send_Temp["door1_ZSO"]     = door1_ZSO;
  JSON_Send_Temp["door1_ZSC"]     = door1_ZSC;
  JSON_Send_Temp["door1_LockSts"] = door1_LockSts;
  JSON_Send_Temp["door2_ZSO"]     = door2_ZSO;
  JSON_Send_Temp["door2_ZSC"]     = door2_ZSC;
  JSON_Send_Temp["door2_LockSts"] = door2_LockSts;
  serializeJson(JSON_Send_Temp, JSON_Send);

  Serial.print("Broadcast JSON Data to Website: ");
  Serial.println(JSON_Send);
  webSocketsServer.broadcastTXT(JSON_Send);
}

void setup() {  
  // GPIO Pin Mode Definitions
  pinMode(pin_wifiReset,    INPUT_PULLUP);  // Wifi Related GPIO
  pinMode(pin_wifiStatus,   OUTPUT);
  
  pinMode(pin_door1CMD,     OUTPUT);        // Door 1
  pinMode(pin_door1Light,   OUTPUT);
  pinMode(pin_door1LockSW,  INPUT);
  pinMode(pin_door1ZSO,     INPUT_PULLUP);
  pinMode(pin_door1ZSC,     INPUT_PULLUP);

  pinMode(pin_door2CMD,     OUTPUT);        // Door 2
  pinMode(pin_door2Light,   OUTPUT);
  pinMode(pin_door2LockSW,  INPUT);
  pinMode(pin_door2ZSO,     INPUT_PULLUP);
  pinMode(pin_door2ZSC,     INPUT_PULLUP);

  // Start Serial Monitor
  Serial.begin(115200);

  // Initialize SPIFFS
  if(!SPIFFS.begin(true)){
    Serial.println("An Error has occurred while mounting SPIFFS");
    return;
  }

  // Initialize / Start WiFi
  wifiInit();

  // If other webpages besides / are requested, syntax would be webServer.on("/page1", HTTP_GET, [](AsyncWebServerRequest * request) - Note the HTTP_GET
  /* webServer.on("/", [](AsyncWebServerRequest * request) {
    request->send(200, "text/html", webpage);
  }); */

  // Route for / web page
  webServer.on("/", HTTP_GET, [](AsyncWebServerRequest *request){
    request->send(SPIFFS, "/index.html", String(), false);  // String(), false, processor instead of webpage
  });
  // Route to Watch Web Page
  webServer.on("/watch", HTTP_GET, [](AsyncWebServerRequest *request){
    
    if(request->hasParam("door")){
      String reqMessage;
      reqMessage = request->getParam("door")->value();
      if(reqMessage == "1") {
        door1_CMD = 1;
      } else if (reqMessage == "2") {
        door2_CMD = 1;
      }
    }
    request->send(SPIFFS, "/index-watch.html", String(), false);  // String(), false, processor instead of webpage
  });
  webServer.on("/style.css", HTTP_GET, [](AsyncWebServerRequest *request){
    request->send(SPIFFS, "/style.css", "text/css");
  });
  // Route to load app.js file
  webServer.on("/app.js", HTTP_GET, [](AsyncWebServerRequest *request){
    request->send(SPIFFS, "/app.js", "text/javascript");
  });
  // Route to favicon
  webServer.on("/favicon.png", HTTP_GET, [](AsyncWebServerRequest *request){
    request->send(SPIFFS, "/favicon.png", "image/png");
  });
  // Route to Locked icon
  webServer.on("/locked", HTTP_GET, [](AsyncWebServerRequest *request){
    request->send(SPIFFS, "/locked.png", "image/png");
  });
  // Route to Unlocked icon
  webServer.on("/unlocked", HTTP_GET, [](AsyncWebServerRequest *request){
    request->send(SPIFFS, "/unlocked.png", "image/png");
  });
  // Route to Blank icon (placeholder for locked / unlocked)
  webServer.on("/blank", HTTP_GET, [](AsyncWebServerRequest *request){
    request->send(SPIFFS, "/blank.png", "image/png");
  });

  AsyncElegantOTA.begin(&webServer);  // Start OTA Server - Navigate to [IP Address]/update to use
  webServer.onNotFound(notFound);
  webServer.begin(); // Start web server
  webSocketsServer.begin(); // Start web sockets server
  webSocketsServer.onEvent(webSocketsEvent);
}

void loop() {
  // WIFI Handling
  if((WiFi.status() == WL_CONNECTED) && (WiFi.getMode() != 2)) {       // Set WiFi Status LED. WiFi.getMode of 2 = AP mode
    digitalWrite(pin_wifiStatus, HIGH);
  } else {
    digitalWrite(pin_wifiStatus, LOW);
  }
  
  unsigned long currentTime = millis();     // Check for WiFi disconnection and attempt to reconnect
  if((WiFi.status() != WL_CONNECTED) && (currentTime - wifi_Previous_Time >= wifi_Reconnect_Delay)) {
    Serial.println("Disconnected from WiFi Network. Attempting to Reconnect");
    WiFi.disconnect();
    WiFi.reconnect();
    wifi_Previous_Time = currentTime;
  }

  if(!digitalRead(pin_wifiReset)) {
    WiFi.disconnect();
    digitalWrite(pin_wifiStatus, LOW);
    wm.resetSettings();
    wifiInit();
  }

  // Websockets Server handling / loop
  webSocketsServer.loop();

  // Listen for Web Page Load Trigger. If received, send JSON data to update status indicators
  if(pageLoadTrigger){
    sendJSONData();
    pageLoadTrigger = 0;
  }

  // Buffer door status before reading values from GPIO
  for (int i = 0; i < 6; i++) {
    doorStatusBuffer[i] = doorStatus[i];
  }
  
  // Process Inputs - Door 1 (invert due to internal pullup for logic purposes)
  door1_LockSts = !digitalRead(pin_door1LockSW);  // Configured as inverted because if signal is not present on GPIO, door is locked
  door1_ZSO     = !digitalRead(pin_door1ZSO);
  door1_ZSC     = !digitalRead(pin_door1ZSC);

  // Process Inputs - Door 2 (invert due to internal pullup for logic purposes)
  door2_LockSts = !digitalRead(pin_door2LockSW);  // Configured as inverted because if signal is not present on GPIO, door is locked
  door2_ZSO     = !digitalRead(pin_door2ZSO);
  door2_ZSC     = !digitalRead(pin_door2ZSC);
  
  // Build input status array
  doorStatus[0] = door1_LockSts; doorStatus[1] = door1_ZSO; doorStatus[2] = door1_ZSC;
  doorStatus[3] = door2_LockSts; doorStatus[4] = door2_ZSO; doorStatus[5] = door2_ZSC;

  // Compare input status array with buffered values. If different, 
  for (int j = 0; j < 6; j++) {
    if (doorStatus[j] != doorStatusBuffer[j]) {
      sendJSONData();
      break;
    }
  }

  if (door1_CMD) {
    digitalWrite(pin_door1CMD, HIGH);
    // One-Shot to set initial time
    if (door1_CMD_Latch != 1) {
      door1_CMD_Time = millis();
    }
    door1_CMD_Latch = 1;
    // Timer to hold output HIGH
    if (millis() - door1_CMD_Time > cmdHoldPeriod) {
      digitalWrite(pin_door1CMD, LOW);
      door1_CMD = 0;
      door1_CMD_Latch = 0;
    } 
  }

  if (door1_Light) {
    digitalWrite(pin_door1Light, HIGH);
    // One-Shot to set initial time
    if (door1_Light_Latch != 1) {
      door1_Light_Time = millis();
    }
    door1_Light_Latch = 1;
    // Timer to hold output HIGH
    if (millis() - door1_Light_Time > cmdHoldPeriod) {
      digitalWrite(pin_door1Light, LOW);
      door1_Light = 0;
      door1_Light_Latch = 0;
    }
  }

  if (door2_CMD) {
    digitalWrite(pin_door2CMD, HIGH);
    // One-Shot to set initial time
    if (door2_CMD_Latch != 1) {
      door2_CMD_Time = millis();
    }
    door2_CMD_Latch = 1;
    // Timer to hold output HIGH
    if (millis() - door2_CMD_Time > cmdHoldPeriod) {
      digitalWrite(pin_door2CMD, LOW);
      door2_CMD = 0;
      door2_CMD_Latch = 0;
    }
  }

  if (door2_Light) {
    digitalWrite(pin_door2Light, HIGH);
    // One-Shot to set initial time
    if (door2_Light_Latch != 1) {
      door2_Light_Time = millis();
    }
    door2_Light_Latch = 1;
    // Timer to hold output HIGH
    if (millis() - door2_Light_Time > cmdHoldPeriod) {
      digitalWrite(pin_door2Light, LOW);
      door2_Light = 0;
      door2_Light_Latch = 0;
    }
  }
}
